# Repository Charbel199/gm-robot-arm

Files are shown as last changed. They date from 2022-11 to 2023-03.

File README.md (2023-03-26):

<p align="center">
  
</p>

--------------------------------------------------------------------

# GM Robot Arm

We are developing a robot arm system that is capable of playing chess. This is just a fun project meant to help us learn new thing.
Here is the simple action flow of the robot arm:
- Take a snapshot of the current chess-board layout using a top-down camera
- Deduce the previous made by the human by comparing the previous and current chessboard layouts using computer vision
- Choose the next best move using a chess engine
- Perform this move through autonomous control of the robot arm

Here is a [video demo](https://www.youtube.com/watch?v=iJfm-6d8eYs) showcasing our robot arm playing a full chess game (And winning).

## Installation

```bash
git clone https://github.com/Charbel199/gm-robot-arm
cd gm-robot-arm
pip install -r ./docker/requirements.txt # Will be later replaced with the actual docker container
```

### Azure Kinect Camera Setup
**Steps to use the azure kinect camera through docker**(_Note: Using the depth camera in docker requires OpenGL which we did not implement yet_)
1) Navigate to the AzureKinect directory
2) Run `. DockerBuild.bash`
3) Wait for the docker image to build 
4) Navigate back to the root of the repo
5) Run `. CameraRun.bash`
6) Using ROS, subscribe to the topic /rgb/image_raw for a BGRA format image 

## How to run it

Run each of the following commands in a separate terminal:
```bash
. CameraRun.bash
python3 ./cores/control_core.py
python3 main.py
```

There are some environment variables which can be set before running `main.py`:

- **USE_CAMERA**: this variable specifies if we want to use the camera or pre-existing images on the system (useful when the camera is not connected)
- **IS_SIMULATION**: this variable allows us to run the robot in simulation mode, where it simply follows a set of predetermined moves instead of evaluating the state of the board and playing the move deduced by the engine.
- **USE_ROBOT**: this variable allows us to run the system without actually using the robotic arm, which is valuable when testing other aspects of the system as the arm is time consuming.
- **WITH_SOUND**: allows the user to mute the clock sound if desired.
- **USE_PREVIOUS_CALIBRATED_BOARD**: this variable allows us to surpass the calibration phase in the case where we are playing in an environment where calibration has already taken place.
- **ENGINE_SIDE**: allows us to choose if the robot is playing as white or black.
- **ELO**: this variable determines what elo the engine will be using (valuable if the user is a beginner and would like to play against someone of the same skill)

To properly use the engine, the following sequence takes place in the gm core:

- Press ‘e’ to calibrate the board (this can be bypassed if the USE_PREVIOUS_CALIBRATED_BOARD environment variable is true). The gm core will then instruct the vision core to calibrate the board based on the current image. This must be done on an empty chess board.
- Press ‘i’ to take a snapshot of the initial board layout. This is important for the vision core to have a base image to start comparing to and figure out what moves were done. Make sure you have placed all the pieces before you press ‘i’.
- Start playing, and press ‘space’ when you complete your move.
  - The robot will make sure that it is the user's turn and that the previous steps (calibration and initialization) are complete.
  - It will launch the chess clock.
  - The gm core instructs the vision core to capture the current image.
  - It then instructs it to compare the previous board image to the current board image and determine which squares changed.
  - It then asks the chess core to determine which move was executed based on which squares changed.
  - It will update the virtual board state.
  - It then switches turn to the robots turn.
- Once it is the robots turn:
  - The gm core retrieves the best move from the chess core based on the current board state.
  - It then asks the chess core to dissect the best move into a sequence of moves that the control core can execute (PICKs, PLACEs, and YEETs)
  - The gm core then sets the control move counter based on how many control moves need to be completed for the entire move to be completed.
  - It then publishes all the moves on the topic that the control core is subscribed to.
  - The gm core waits until the move is fully executed (move counter is 0)
  - The gm core instructs the vision core to capture the current image.
  - It then instructs the chess core to update the virtual board.
  - Finally, it switches back to the user’s turn.

Some other features that can be done are pressing ‘v’ to visualize the last move as determined by vision and to press ‘b’ to visualize all images that the vision core is using. 

The final feature is the ‘esc’ key that allows us to reset the cores and start a game from scratch.

--------------------------------------------------------------------

## General architecture

The system is divided into **4 main components**: Chess core, vision core, control core and gm core. Each core has a set
of unique functionalities which we will discuss further in later parts.



Here is a communication diagram showing how the various components communicate with each other:

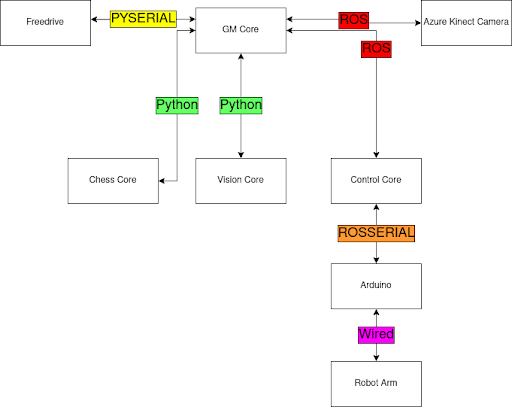
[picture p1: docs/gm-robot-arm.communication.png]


## Software Components

- Stockfish
- ROS
- OpenCV

## Hardware Components

- [6 DOF Robot arm (LeArm)](https://www.hiwonder.com/store/learn/2.html)
- Azure Kinect camera
- Arduino Mega 2560

_Note: The robotic arm used is intended for educational purposes, therefore, its servos are not the most accurate.
It would obviously have been better to use a more precise and expensive arm for better results._

_Note 2: The Azure kinect camera is way overkill for this project, but it was the camera we had at hand._

## Chess pieces

There chess pieces were designed on SOLIDWORK, here is a picture of the bishop 3d model:

<p align="center">
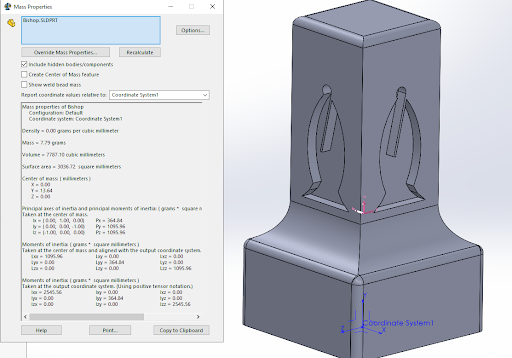
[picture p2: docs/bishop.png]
  
</p>

## Cores

### Chess Core

The chess core has two main functionalities:
- Visualize the current board layout
- Load a chess engine to generate moves for the robotic arm

Our chess visualizer makes use of the python **“chess”** package which 
provides us with a miniature **chess board svg** and can be fed moves 
to update the svg. We are using the resulting image to track the piece positions during the game.

<p align="center">
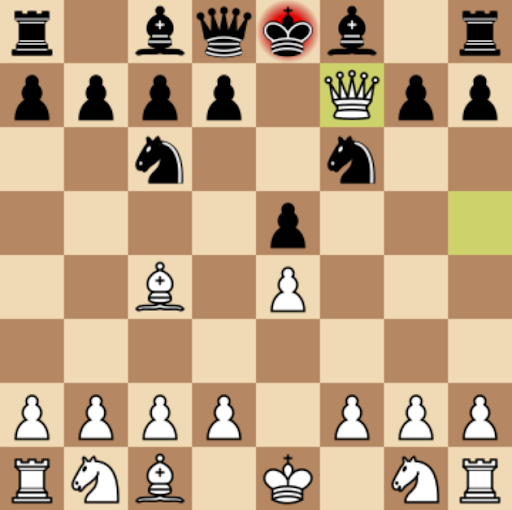
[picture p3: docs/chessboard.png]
  
</p>

### Vision Core

The main tasks of the vision core are to analyze the physical chess board, deduce the player’s move, and keep the chess pieces’ positions up to date.
We will briefly discuss the main functions that were implemented in the vision core:

- Preprocess image: This function is called each time we capture a new image. Based on the 4 markers in the corners of the chess board, it determines their coordinates and warps the image so that the chessboard is the only part of the image that is left.

<p align="center">
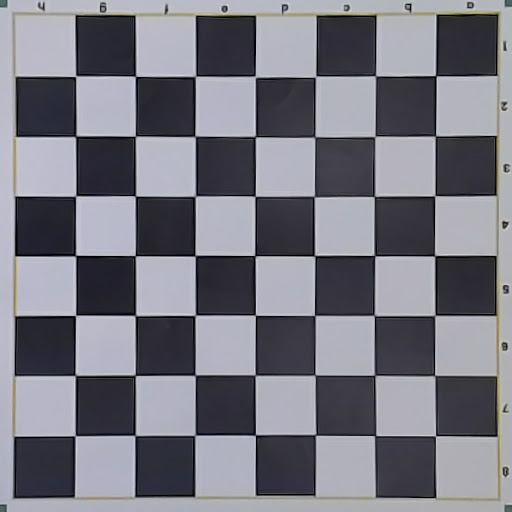
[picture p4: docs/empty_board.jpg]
  
</p>

- Visualize all images: Show up to the last 7 chess board snapshots (each representing a move) along with the calibrated board image.
- Visualize last move: Visualize the last 2 chess board snapshots with the move performed highlighted in red
- Calibrate: Uses the HSV threshold specified in the config json file located in the “assets/hsv” folder, the Vision core obtains the squares information after some image processing:
  - Get HSV filtered canny edges for white squares
  - Get HSV filtered canny edges for black squares
  - Combine both edge images
  <p align="center">
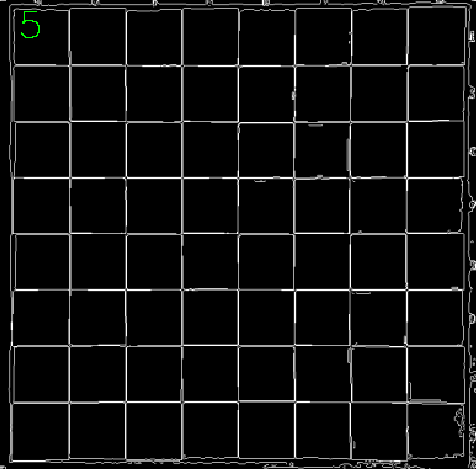
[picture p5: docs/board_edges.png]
    
  </p>
  
  - Perform Gaussian blur and threshold

  <p align="center">
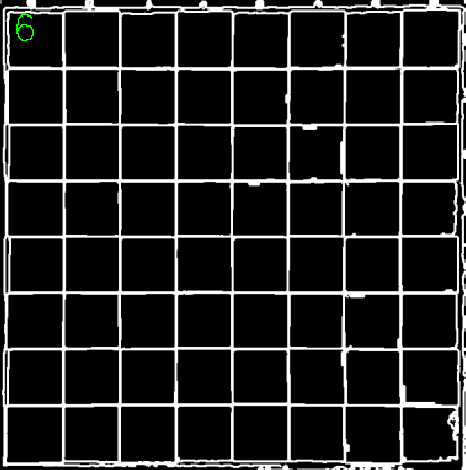
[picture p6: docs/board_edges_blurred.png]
    
  </p>

  - Find all possible contours and filter them based on the board size (We are assuming that each square has a minimum area of: (Wboard * Hboard / 64) and a maximum area of: minimum area * 1.3)

  <p align="center">
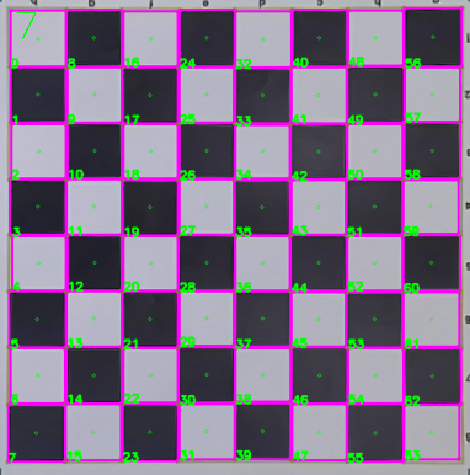
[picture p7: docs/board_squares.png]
    
  </p>

  - Reduce points meaning that since each square has 4 corners, many points will overlap, this step combines points that are very close to each other

- Capture image: Record the current image from the camera (Recorded through ROS in GM core
- Update images: Update the list of image (Keep the 7 most recent snapshots)
- Capture initial chess board layout: Set the next recorded image as the “Initial board layout” snapshot
- Get user squares changed: To deduce which squares have changed between the last 2 recorded snapshots, the vision core extracts color features from each square of both images and compares them, based on this comparison it can accurately determine which squares have changed. To explain this concept further: It is very inefficient to try to determine the type of piece that is present on each square on the board, alternatively, we are determining the DIFFERENCE between every 2 snapshots, and since we have a constant record of the pieces’ locations on the chess board, the system is able to deduce the next position on the chess board. (This is similar to how GITHUB works where each ‘delta’/difference is recorded with each commit and we are able to rollback to any previous version by simply reversing commits)
<p align="center">
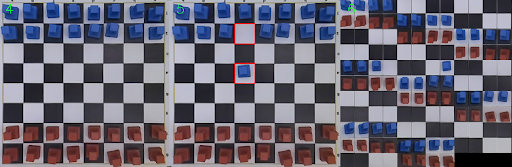
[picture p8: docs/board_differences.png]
  
</p>
Here is a screenshot showing the visualization generated by the vision core module:
<p align="center">
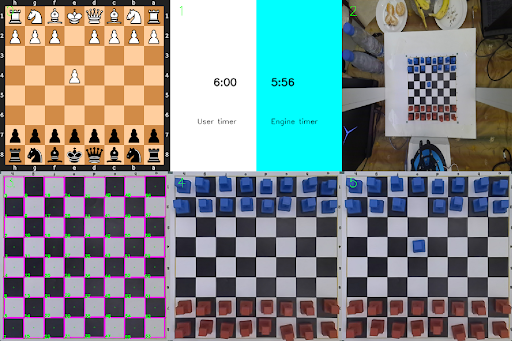
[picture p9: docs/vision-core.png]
  
</p>

### Control Core

The control core is mainly responsible for controlling the robotic arm. This core receives the move it's supposed to make on a rostopic in a custom message type called Move. This message contains two variables: type and square. The possible types are:

- PICK: specifies that we want the arm to pick the piece in the square.
- PLACE: specifies that we want the arm to place the piece it is carrying in the square.
- YEET: specifies that we want the arm to discard the piece it is carrying (used for taking a piece).

The square is simply a chess board square specified as ‘letterNumber’ such as ‘a5’.

The control core then accesses a python dictionary containing the sequence of moves that must be taken to go to a specific square. This dictionary has chess squares as its keys and a list of servo positions as its values. 

The core then publishes these servo positions onto a rostopic as a custom message type called ServoPositions. These positions are then written to the servos by arduino. The exact communication will be discussed in a later section. 

Let us take a full example of how the control core functions:

Consider that the chess core determines that the best move is for the pawn on square e5 to take the pawn on d4, the Move messages published by the gm core would be:

1) PICK D4
2) YEET 
3) PICK E5
4) PLACE D4

The control core would thus start with the message: [‘PICK’, ‘d4’]. It would access the move dictionary to know the servo positions corresponding to d4, and start publishing these positions to the arduino for the robot arm to move to d4. The type ‘PICK’ helps us determine that the gripper should be open initially, and should close once we are in the position d4. At the end of this move, we expect the arm to now have the pawn at d4 in its gripper.

Afterwards, the control core proceeds with the message [‘YEET’,’’]. This means that the arm will now simply go to the predetermined YEET_POSE and release the pawn it is carrying there.

Then, the control core processes the message [‘PICK’, ‘e5’]. Thus, the robotic arm is expected to go to square e5 and pick up the pawn there.

Finally, the control core proceeds with the last message [‘PLACE’, ‘d4’] in which it will place the pawn it is currently carrying on square d4, meaning the entire move is completed. At this point, the robotic arm will return to its SAFE_POSE which is a position that is away from the board and doesn’t impede the camera's field of view.

_Note that the arduino is publishing constantly to a topic to inform the control core it is done with the positions that were last sent to it, this allows the control core to send the other move. Additionally, the control core decrements a global parameter everytime a move is completed which helps the gm core determine if the entire move has been completed. In the previous example, this counter would be 4, and the control core will decrement it after every sequence, and once all 4 have been completed the gm core knows that the entire move is executed and can thus proceed._

### GM Core

The GM core, or the grandmaster core, is the “brain” of the robot. Its main function is to create and connect the other 3 cores and transmit messages between them.  It also creates the menu to be used by the user and takes his inputs through a keylogger. 

All the functionalities of the GM core were discussed in the [How to run it](#how-to-run-it) section where the environment variables and keyboard inputs were discussed. 

## Developers

- [Charbel Bou Maroun](https://github.com/Charbel199)
- [Georges Daou](https://github.com/George1044)
- [Ralph Sakhat](https://github.com/Ralph-S)

## License
This project is licensed under the MIT License. See the LICENSE file for details.

## Acknowledgements

We would like to thank [3D Maker shop](https://www.3dmakershop.com/) for sponsoring our project and helping us print all the chess pieces that we used.

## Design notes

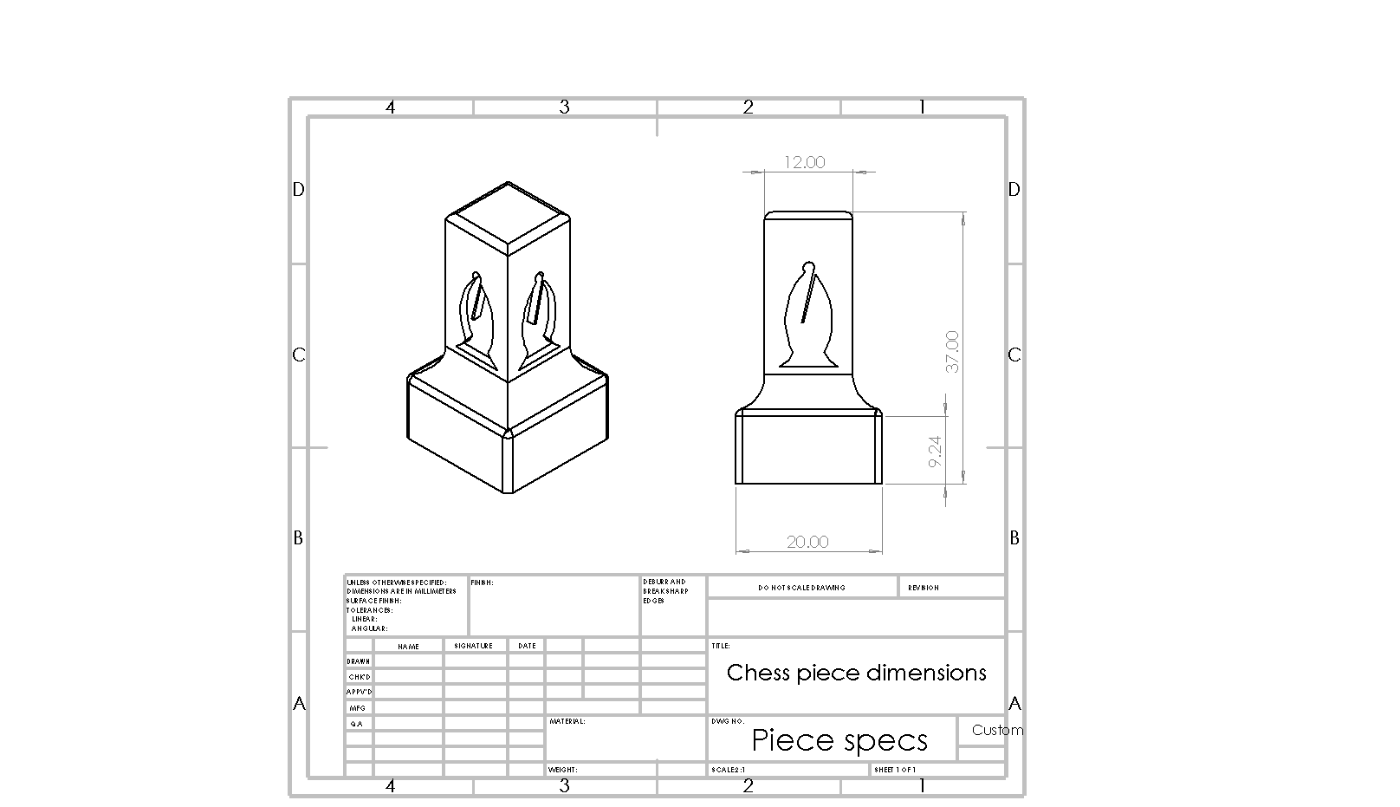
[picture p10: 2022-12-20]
src/arm/CAD/Chess pieces/Profiles/Piece specs.PNG

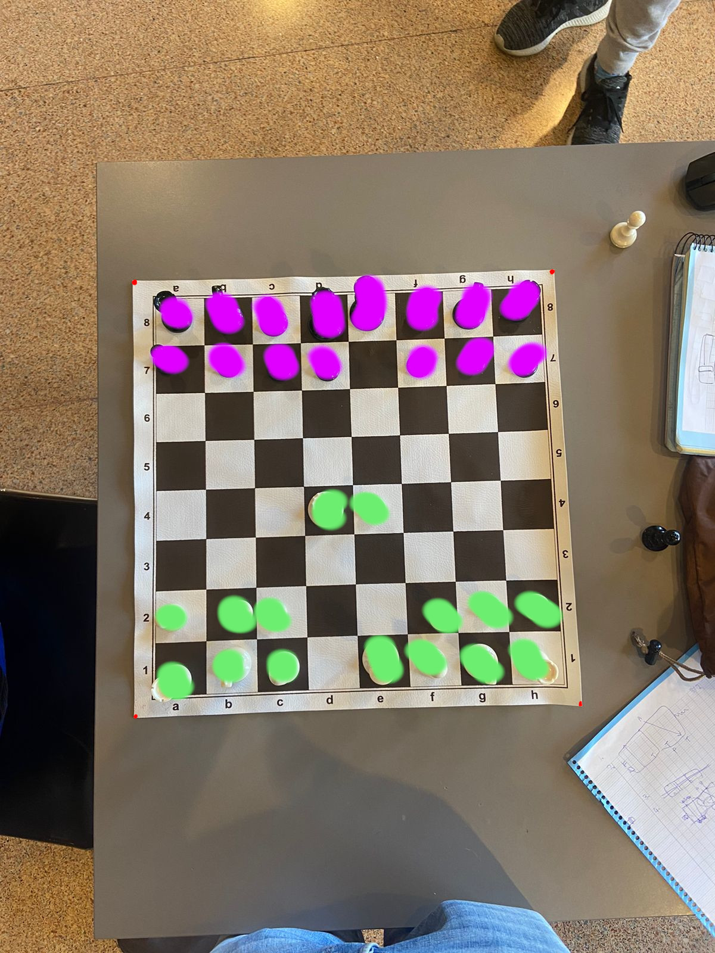
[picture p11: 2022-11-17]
src/assets/moves/real_board/colored/Move5.jpeg

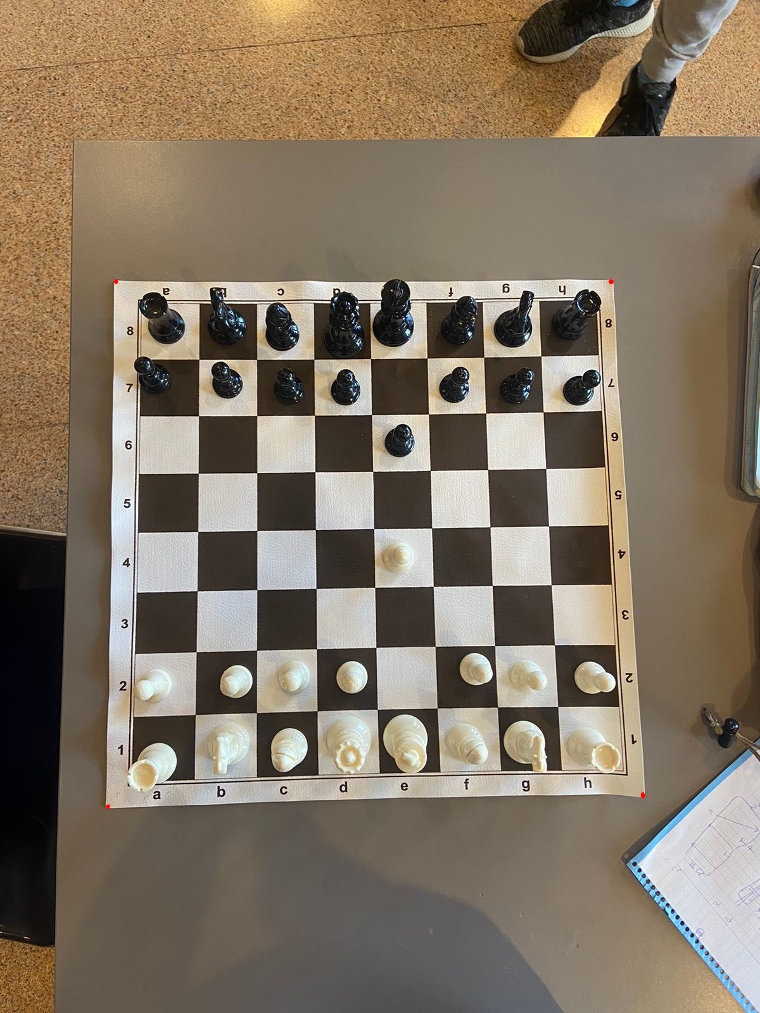
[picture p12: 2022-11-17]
src/assets/moves/real_board/Move2.jpeg

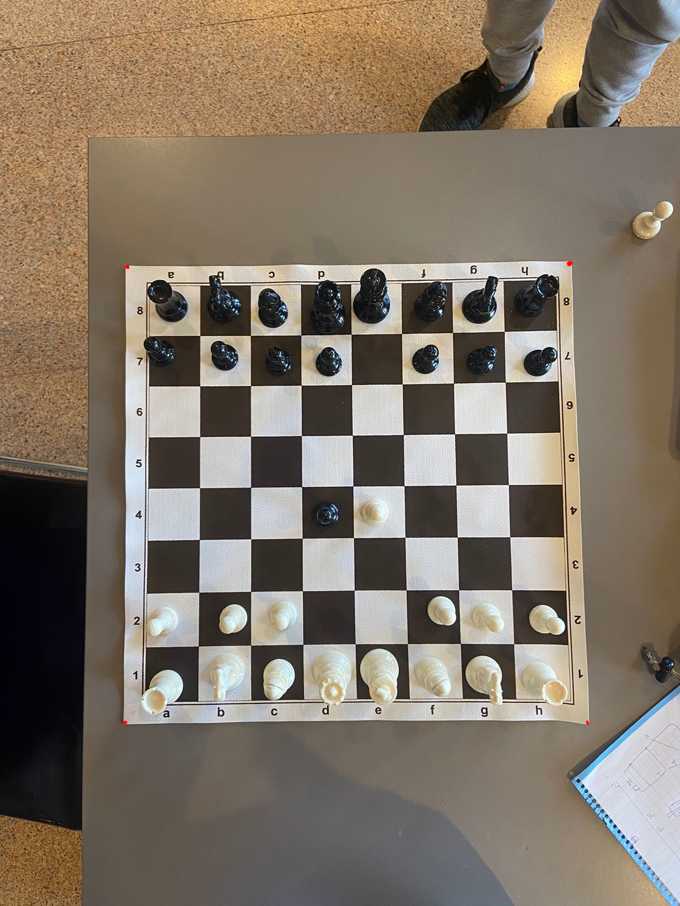
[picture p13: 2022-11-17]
src/assets/moves/real_board/Move4.jpeg

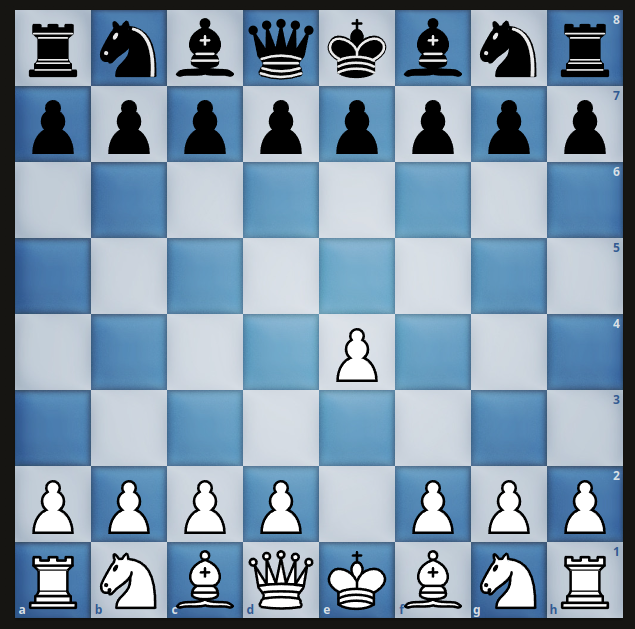
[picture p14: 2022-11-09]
src/assets/moves/lichess_2.png

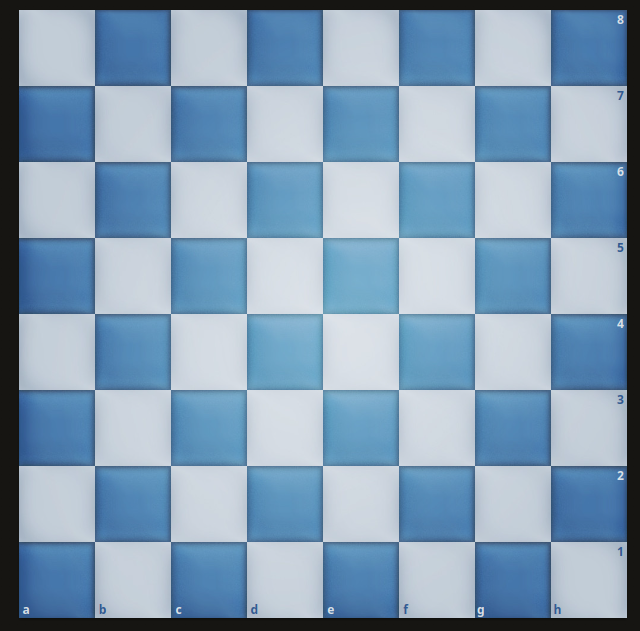
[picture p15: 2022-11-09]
src/assets/moves/empty_lichess2.png

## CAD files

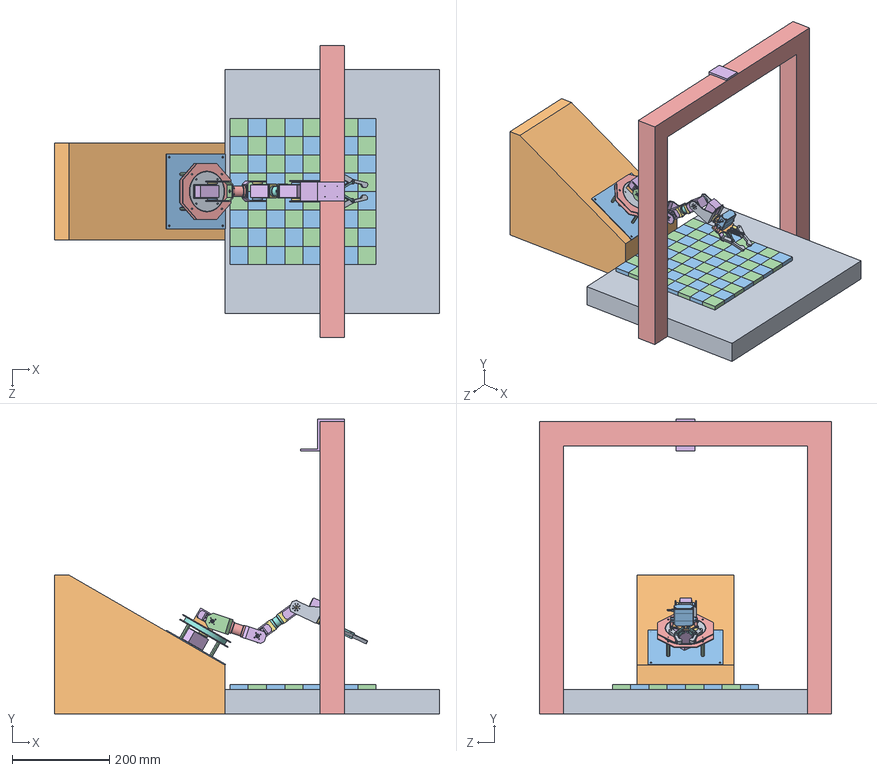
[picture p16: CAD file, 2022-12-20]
src/arm/CAD/Complete Assembly/Project Assembly.SLDASM
790.0 x 605.0 x 600.0 mm
BaseAssembly
RobotBase
BasePlate
SpacerNut x 4
RotaryAxisPolygonPlate x 2
LX-15D-LOBOT SERVO LEWANSOUL x 5
FrontHub x 6
RotaryAxisBearing
RotaryAxisDiskPlate x 2
LongServoSideBracket
BackHub x 3
Lower Pitch Bracket
29mm Union
Mid Pitch Bracket
ShortServoSideBracket x 2
20.5mm Union
Upper Pitch Bracket
GripperBasePlate
Lewansoul_LD-27MG Servo
M3 2.5mm length Spacer x 3
M3 11mm length Spacer x 4
GripperServoArmRightSide
GripperServoArmLeftSide
finger dog bone x 4
EndFinger x 4
ServoGriperHeadToGripperBaseBracket x 2
Black squares
White squares
CameraBase
CameraHolder

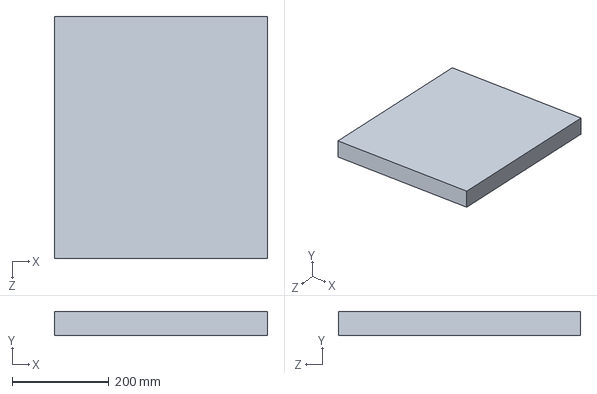
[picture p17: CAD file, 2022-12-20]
src/arm/CAD/Environment base/BaseAssembly.SLDPRT
440.0 x 50.0 x 500.0 mm

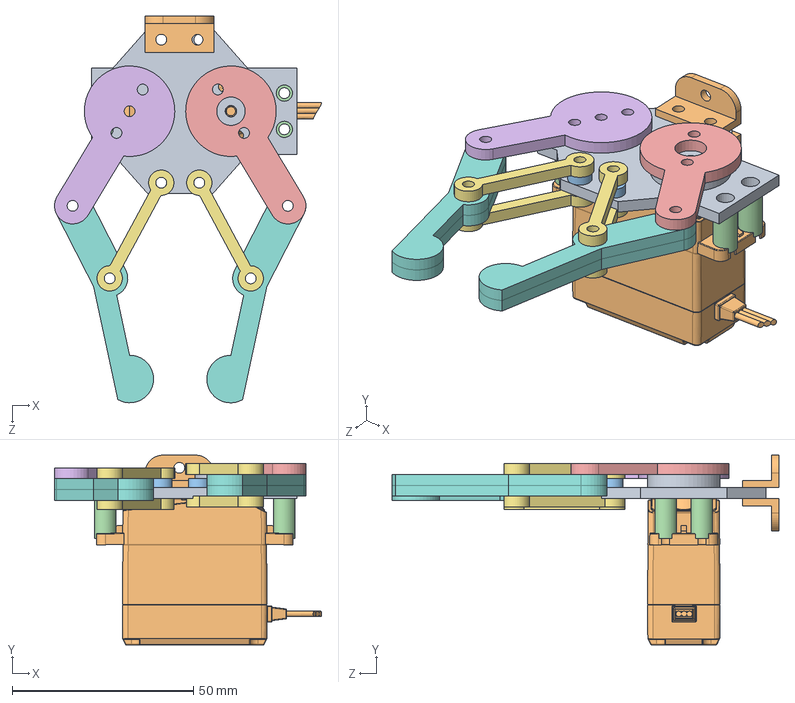
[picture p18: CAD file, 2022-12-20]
src/arm/CAD/robot assembly/GripperAssy.SLDASM
73.7 x 52.4 x 106.8 mm
GripperBasePlate
Lewansoul_LD-27MG Servo
M3 2.5mm length Spacer x 3
M3 11mm length Spacer x 4
GripperServoArmRightSide
GripperServoArmLeftSide
finger dog bone x 4
EndFinger x 4
FrontHub
ServoGriperHeadToGripperBaseBracket x 2

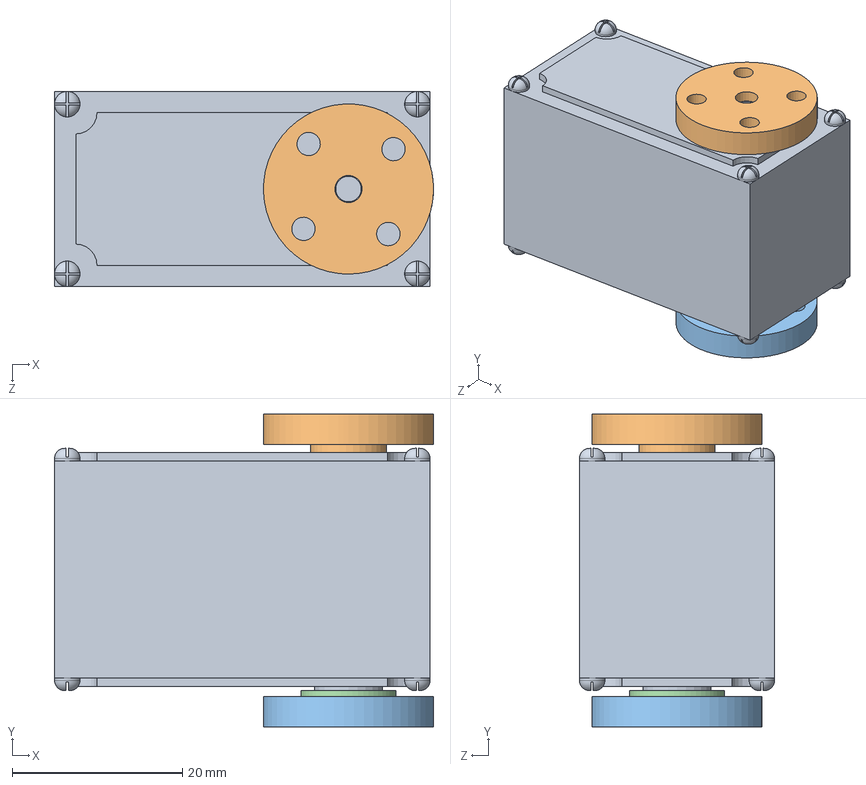
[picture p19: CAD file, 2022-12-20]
src/arm/CAD/robot assembly/LX-15D LOBOT Servo 2-Horns Assy.SLDASM
44.6 x 36.8 x 22.9 mm
LX-15D-LOBOT SERVO LEWANSOUL
FrontHub
BackHub
Bearing

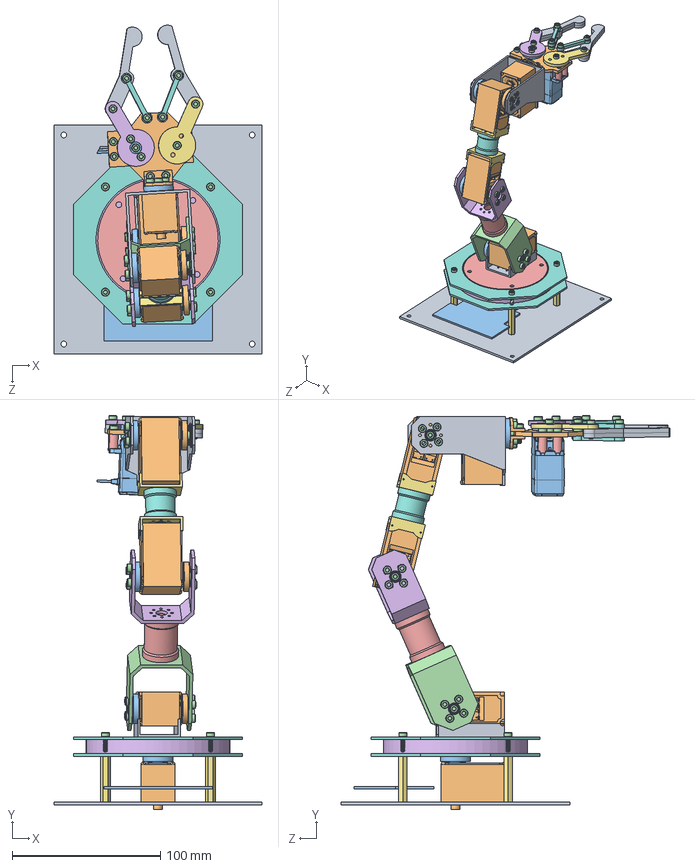
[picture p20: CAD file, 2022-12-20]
src/arm/CAD/robot assembly/LewanSoul LOBOT Arm Assy.SLDASM
140.3 x 265.8 x 221.8 mm
BasePlate
LX-15D-LOBOT SERVO LEWANSOUL x 5
FrontHub x 6
M3 5.5mm x 62
RotaryAxisDiskPlate x 2
RotaryAxisBearing
SpacerNut x 4
RotaryAxisPolygonPlate x 2
LongServoSideBracket
BackHub x 3
Bearing x 3
Lower Pitch Bracket
29mm Union
Mid Pitch Bracket
ShortServoSideBracket x 2
20.5mm Union
Upper Pitch Bracket
GripperBasePlate
Lewansoul_LD-27MG Servo
M3 2.5mm length Spacer x 3
M3 11mm length Spacer x 4
GripperServoArmRightSide
GripperServoArmLeftSide
finger dog bone x 4
EndFinger x 4
ServoGriperHeadToGripperBaseBracket x 2
ArmControllerBoard

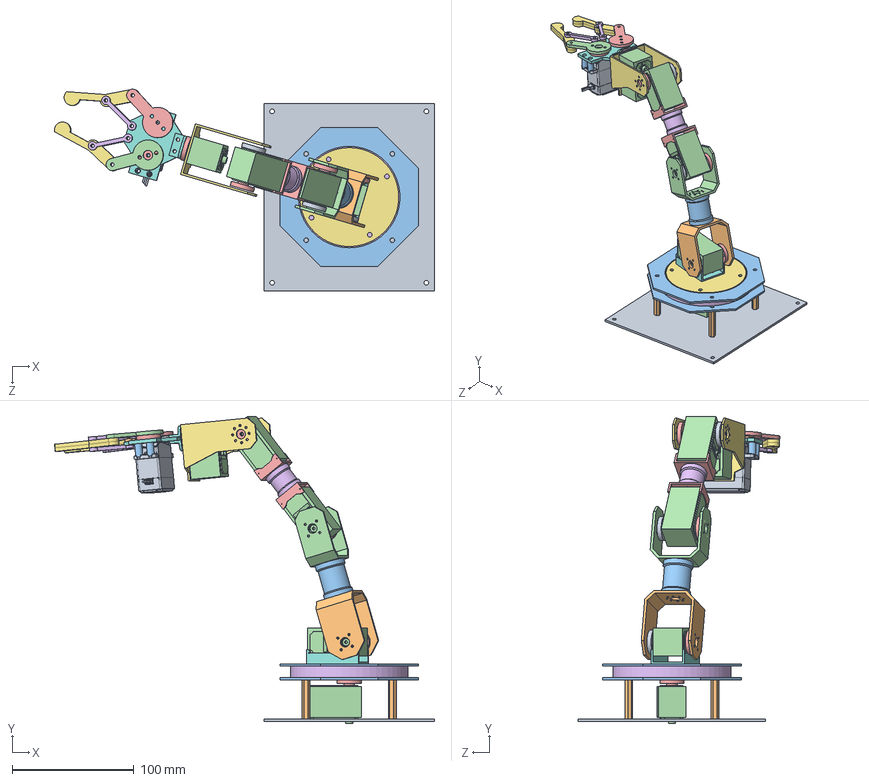
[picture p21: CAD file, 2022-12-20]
src/arm/CAD/Robot Arm Assembly/NewAssembly.SLDASM
312.7 x 252.9 x 165.9 mm
BasePlate
SpacerNut x 4
RotaryAxisPolygonPlate x 2
LX-15D-LOBOT SERVO LEWANSOUL x 5
FrontHub x 6
RotaryAxisBearing
RotaryAxisDiskPlate x 2
LongServoSideBracket
BackHub x 3
Lower Pitch Bracket
29mm Union
Mid Pitch Bracket
ShortServoSideBracket x 2
20.5mm Union
Upper Pitch Bracket
GripperBasePlate
Lewansoul_LD-27MG Servo
M3 2.5mm length Spacer x 3
M3 11mm length Spacer x 4
GripperServoArmRightSide
GripperServoArmLeftSide
finger dog bone x 4
EndFinger x 4
ServoGriperHeadToGripperBaseBracket x 2

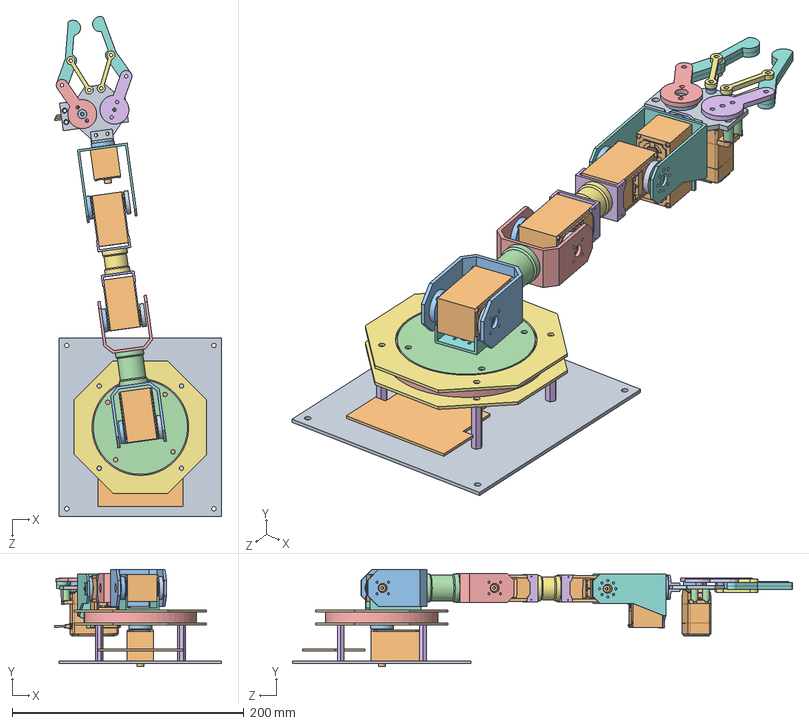
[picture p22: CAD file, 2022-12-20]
src/arm/CAD/robot assembly/LewanSoul LOBOT Arm Assy at legth.SLDASM
144.4 x 84.0 x 431.6 mm
BasePlate
LX-15D-LOBOT SERVO LEWANSOUL x 5
FrontHub x 6
RotaryAxisDiskPlate x 2
RotaryAxisBearing
SpacerNut x 4
RotaryAxisPolygonPlate x 2
LongServoSideBracket
BackHub x 3
Bearing x 3
Lower Pitch Bracket
29mm Union
Mid Pitch Bracket
ShortServoSideBracket x 2
20.5mm Union
Upper Pitch Bracket
GripperBasePlate
Lewansoul_LD-27MG Servo
M3 2.5mm length Spacer x 3
M3 11mm length Spacer x 4
GripperServoArmRightSide
GripperServoArmLeftSide
finger dog bone x 4
EndFinger x 4
ServoGriperHeadToGripperBaseBracket x 2
ArmControllerBoard

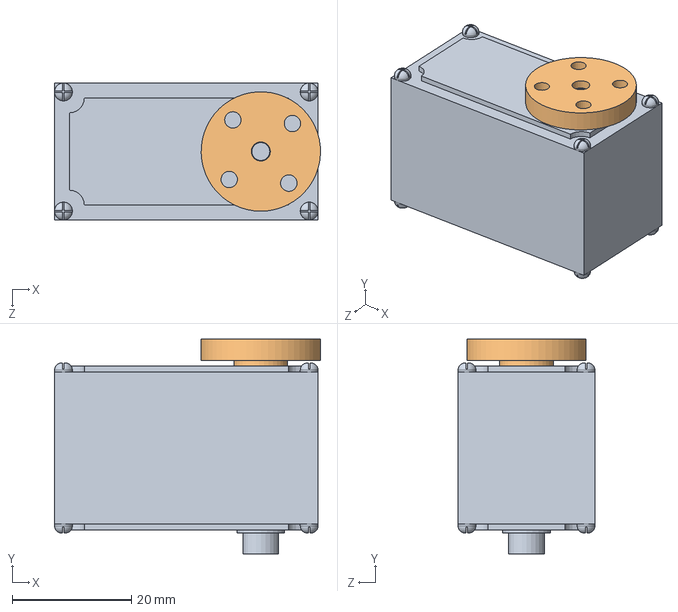
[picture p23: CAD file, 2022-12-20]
src/arm/CAD/robot assembly/LX-15D LOBOT Servo 1-Horn Assy.SLDASM
44.6 x 36.0 x 22.9 mm
LX-15D-LOBOT SERVO LEWANSOUL
FrontHub

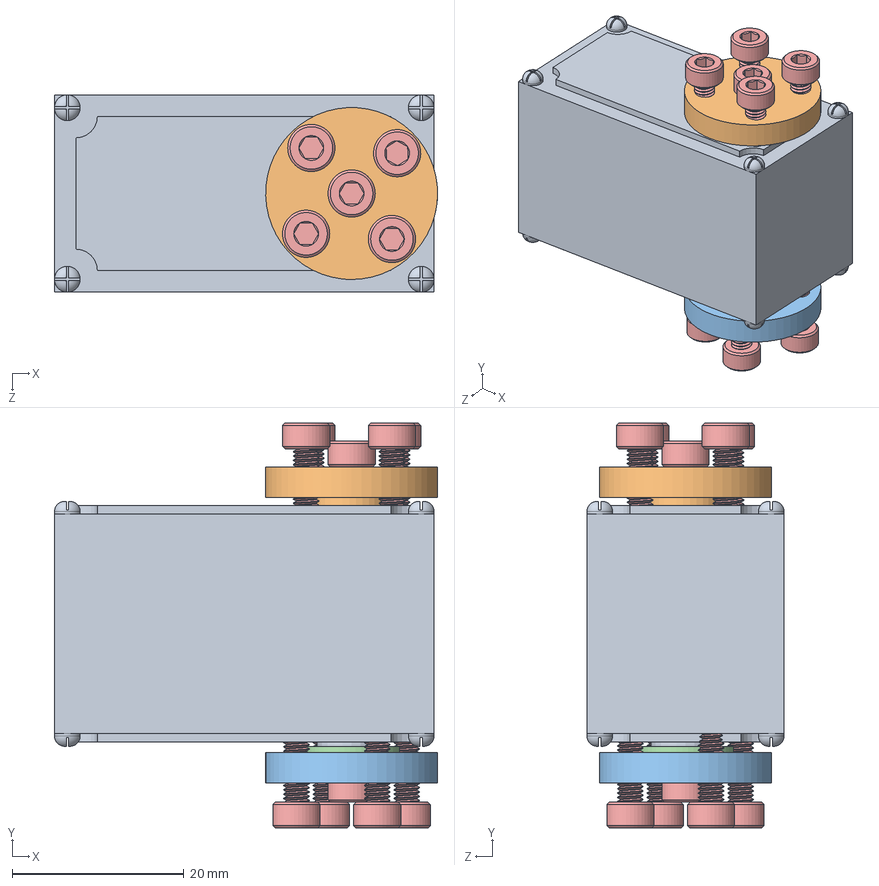
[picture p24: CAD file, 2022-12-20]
src/arm/CAD/robot assembly/LX-15D LOBOT SERVO ASSY.SLDASM
44.6 x 47.1 x 22.9 mm
LX-15D-LOBOT SERVO LEWANSOUL
FrontHub
BackHub
Bearing
M3 5.5mm x 10

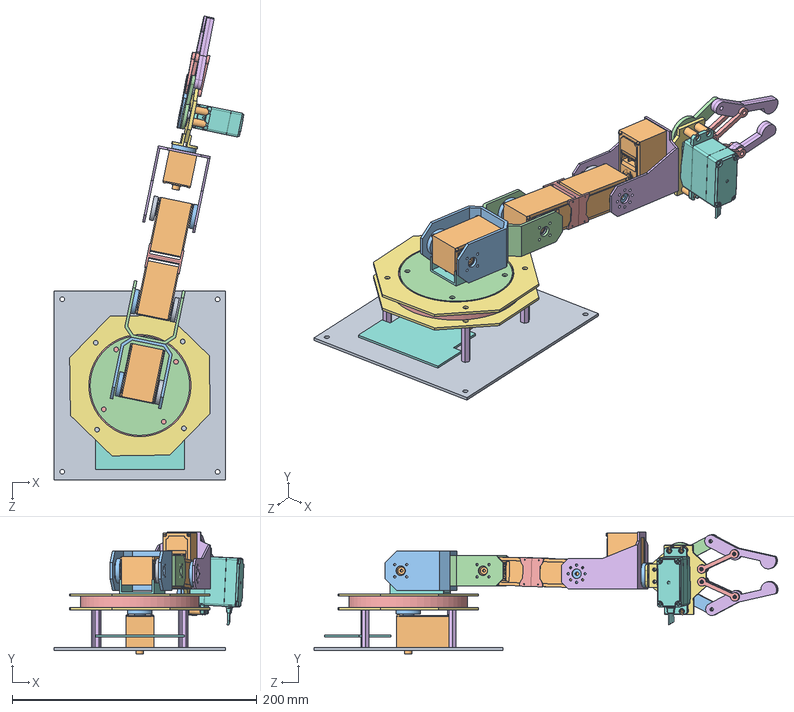
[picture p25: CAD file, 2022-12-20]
src/arm/CAD/robot assembly/LewanSoul LOBOT Arm Assy modified union parallel.SLDASM
155.2 x 99.5 x 379.2 mm
BasePlate
LX-15D-LOBOT SERVO LEWANSOUL x 5
FrontHub x 6
RotaryAxisDiskPlate x 2
RotaryAxisBearing
SpacerNut x 4
RotaryAxisPolygonPlate x 2
LongServoSideBracket
BackHub x 3
Bearing x 3
Lower Pitch Bracket
Mid Pitch Bracket
ShortServoSideBracket x 2
Upper Pitch Bracket
GripperBasePlate
Lewansoul_LD-27MG Servo
M3 2.5mm length Spacer x 3
M3 11mm length Spacer x 4
GripperServoArmRightSide
GripperServoArmLeftSide
finger dog bone x 4
EndFinger x 4
ServoGriperHeadToGripperBaseBracket x 2
ArmControllerBoard

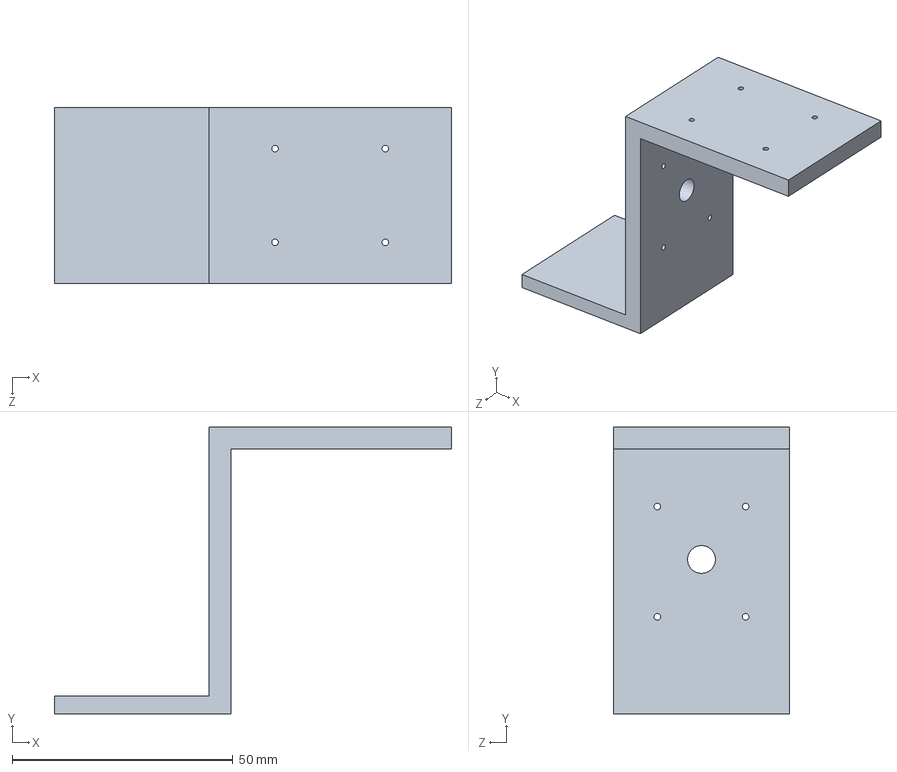
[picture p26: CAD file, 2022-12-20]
src/arm/CAD/Camera Holder/CameraHolder.SLDPRT
90.0 x 65.0 x 40.0 mm

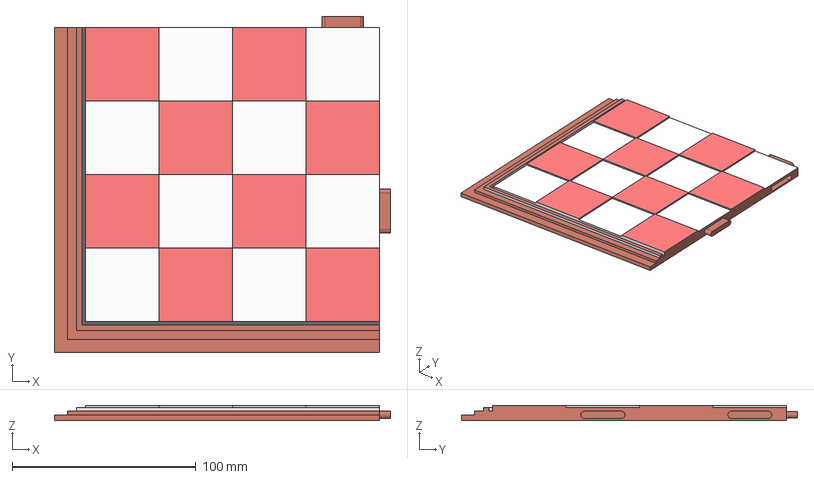
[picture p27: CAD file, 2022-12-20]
src/arm/CAD/chess board/chess board 2 (x2).stp
183.0 x 183.0 x 8.00 mm

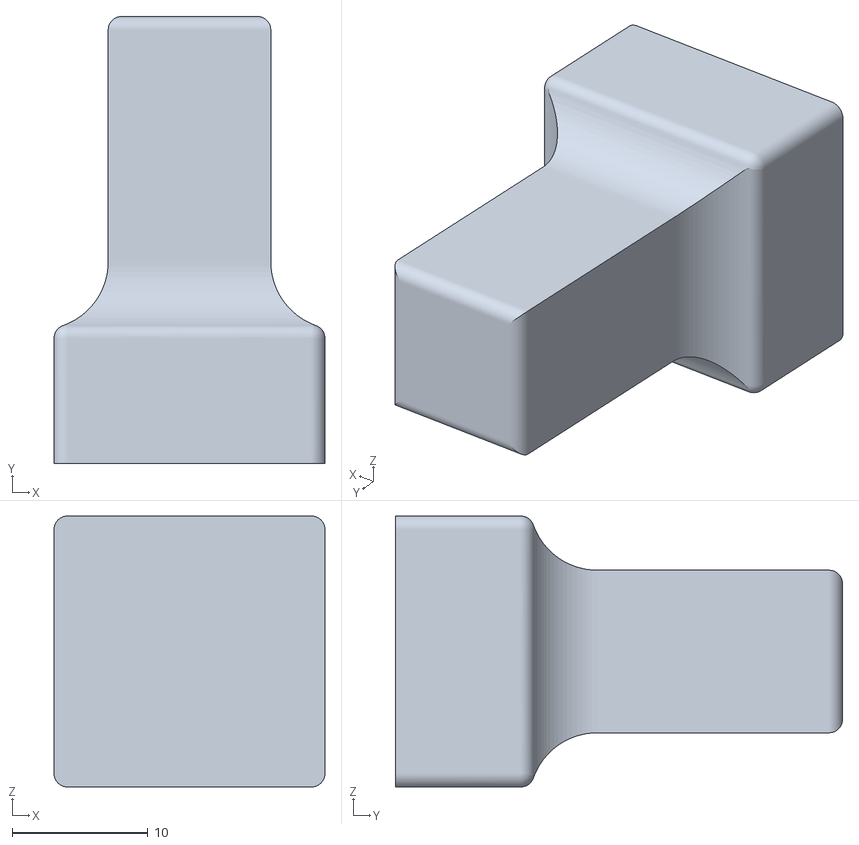
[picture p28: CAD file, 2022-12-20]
src/arm/CAD/Chess pieces/ChessPiece12-33.STL
20.0 x 33.0 x 20.0

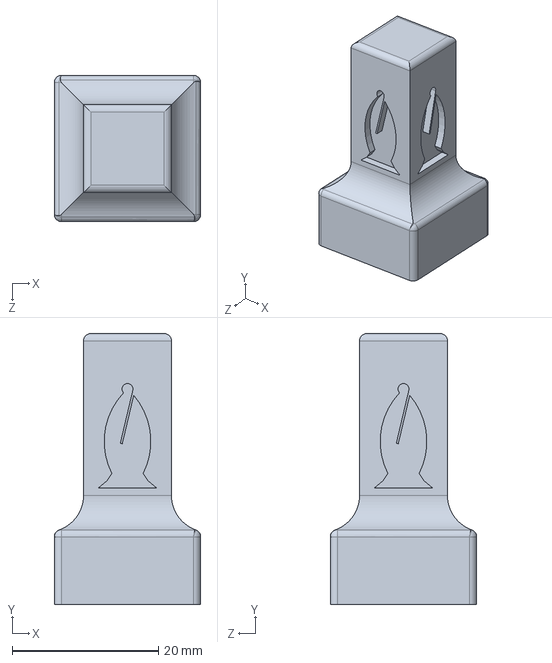
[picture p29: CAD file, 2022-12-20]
src/arm/CAD/Chess pieces/Profiles/Bishop.SLDPRT
20.0 x 37.0 x 20.0 mm

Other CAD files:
src/arm/CAD/New Chess Board/White squares.SLDPRT
src/arm/CAD/Robot Arm Assembly/BackHub .SLDPRT
src/arm/CAD/robot assembly/ShortServoSideBracket.SLDPRT
src/arm/CAD/Camera Holder/CameraBase.SLDPRT
src/arm/CAD/Camera Holder/CameraHolder.STL
src/arm/CAD/Chess pieces/ChessPiece.SLDPRT
src/arm/CAD/Chess pieces/ChessPiece12-35.STL
src/arm/CAD/Chess pieces/ChessPiece12-37.STL
src/arm/CAD/Chess pieces/ChessPiece33.STL
src/arm/CAD/Chess pieces/ChessPiece35.STL
src/arm/CAD/Chess pieces/ChessPiece37.STL
src/arm/CAD/Chess pieces/GenericPiece.SLDDRW
src/arm/CAD/Chess pieces/GenericPiece.SLDPRT
src/arm/CAD/Chess pieces/GenericPiece.STL
src/arm/CAD/Chess pieces/Profiles/Bishop.STL
src/arm/CAD/Chess pieces/Profiles/Caballo ajedrez 2D.dwg
src/arm/CAD/Chess pieces/Profiles/King.SLDPRT
src/arm/CAD/Chess pieces/Profiles/King.STL
src/arm/CAD/Chess pieces/Profiles/Knight.SLDPRT
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

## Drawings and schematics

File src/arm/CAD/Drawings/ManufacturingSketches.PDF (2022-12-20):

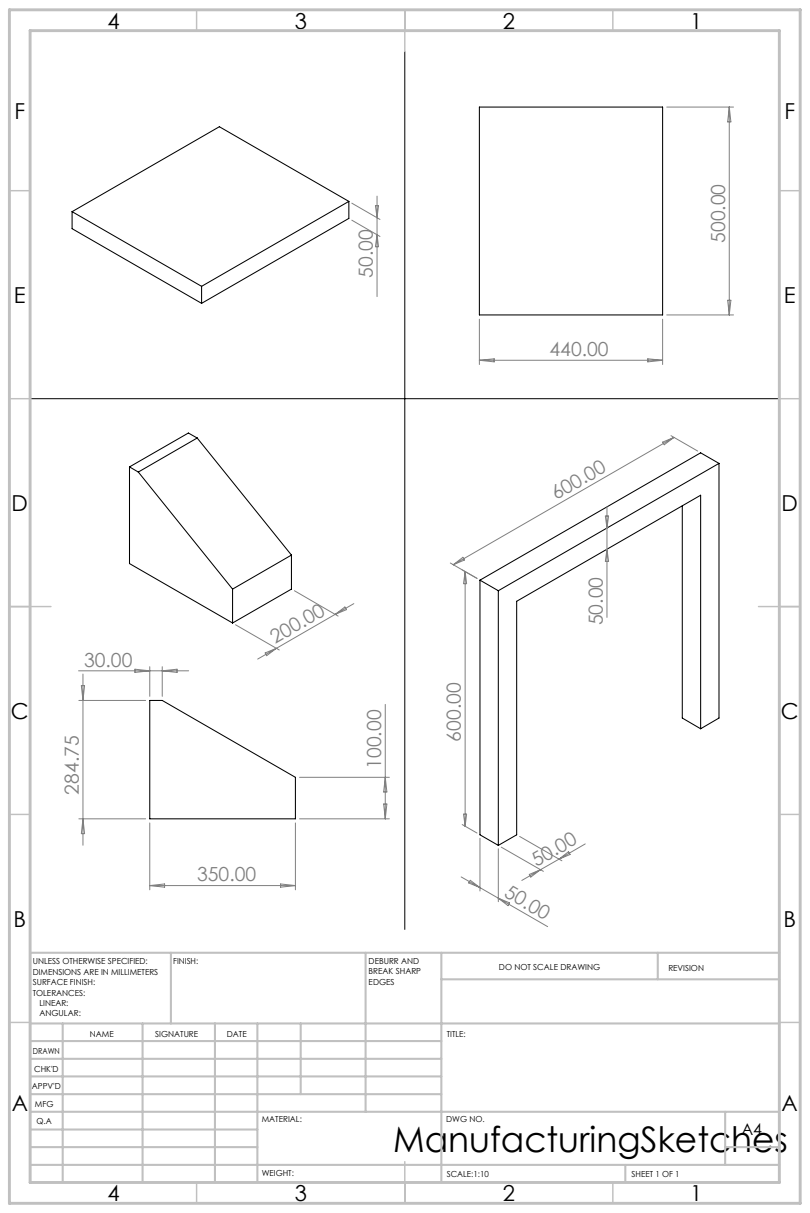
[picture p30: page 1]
FINISH:; DEBURR AND; BREAK SHARP; DO NOT SCALE DRAWING; REVISION; SCALE:1:10; SHEET 1 OF 1

UNLESS OTHERWISE SPECIFIED:
DIMENSIONS ARE IN MILLIMETERS
SURFACE FINISH:
TOLERANCES:
LINEAR:
ANGULAR:

NAME | SIGNATURE | DATE | | | | TITLE:

DRAWN
CHK'D
APPV'D
MFG
Q.A | | | | MATERIAL: ManufacturingSketches | DWG NO. | A4

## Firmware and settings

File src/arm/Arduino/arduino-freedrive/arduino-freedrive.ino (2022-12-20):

#include <Servo.h>
#define servoPin1 7
#define servoPin2 2
#define servoPin3 3
#define servoPin4 4
#define servoPin5 5
#define servoPin6 6

Servo servo1;   //Range: 90 to 180
Servo servo2;   //Range: 0 to 180
Servo servo3;   //Range: 0 to 180 
Servo servo4;   //Range: 0 to 180
Servo servo5;   //Range: 0 to 180
Servo servo6;   //Range: 0 to 180

#define DELAY 5
#define SERVO_STEP 5
#define SERVO_STEP_SMALL 2

#define servo1_safe 146
#define servo2_safe 0
#define servo3_safe 90
#define servo4_safe 0
#define servo5_safe 180
#define servo6_safe 90

int x;
String instruction;
String str;
char move_instruction;
float servo1_pos;
float servo2_pos;
float servo3_pos;
float servo4_pos;
float servo5_pos;
float servo6_pos;
int servo;
String servo_positions = "";
int value;


void setup() {
  Serial.begin(9600);
  pinMode(13, OUTPUT);
  servo1.attach(servoPin1);
  servo1.write(servo1_safe);
  servo2.attach(servoPin2);
  servo2.write(servo2_safe);
  servo3.attach(servoPin3);
  servo3.write(servo3_safe);
  servo4.attach(servoPin4);
  servo4.write(servo4_safe);
  servo5.attach(servoPin5);
  servo5.write(servo5_safe);
  servo6.attach(servoPin6);
  servo6.write(servo6_safe);
  Serial.setTimeout(1);
}

void loop() {
  free_drive_control();
}

void moveServo(Servo servoX, int from, int to, int delayValue){
  if(to>=0 && to<=180){
    if(from > to){
        for(int i=from; i>to; i--){
            servoX.write(i);
            delay(delayValue);
            }
           }


  if(from < to){
  for(int i=from; i<to; i++){
    servoX.write(i);
    delay(delayValue);
  }
  }
  }
}


void manual_control(){
 while (!Serial.available());      // Loop till arduino receives a message
  instruction = Serial.readString();
  servo1_pos = servo1.read();
  servo2_pos = servo2.read();
  servo3_pos = servo3.read();
  servo4_pos = servo4.read();
  servo5_pos = servo5.read();
  servo6_pos = servo6.read();

  if(instruction == "R"){
      digitalWrite(13,HIGH);
      delay(250);
      digitalWrite(13,LOW);
      delay(250);
      servo_positions = "";
      servo_positions = servo_positions + "Servo 1: " + servo1_pos + "\t[" + servo2_pos + ", " + servo3_pos + ", " + servo4_pos + ", " + servo5_pos + ", " + servo6_pos +"]"; //stupid arduino string concatenation
      Serial.println(servo_positions);
    }
  else if(instruction == "W"){
      digitalWrite(13,HIGH);
      delay(250);
      digitalWrite(13,LOW);
      delay(250);
      while (!Serial.available()); //waiting for servo
      str = Serial.readString();
      //servo = str.toInt();
      servo = 1;
      Serial.println("Moving servo " + str);
      while (!Serial.available()); //waiting for angle
      str = Serial.readString();
      //value = str.toInt();
      value = 120;
      Serial.println("Going to angle " + str);
      switch(servo) {
        case 1: moveServo(servo1, servo1_pos, value, DELAY);
        break;
        case 2: moveServo(servo2, servo2_pos, value, DELAY);
        break;
        case 3: moveServo(servo3, servo3_pos, value, DELAY);
        break;
        case 4: moveServo(servo4, servo4_pos, value, DELAY);
        break;
        case 5: moveServo(servo5, servo5_pos, value, DELAY);
        break;
        case 6: moveServo(servo6, servo6_pos, value, DELAY);
        break;
        default:
        break;
        }
      Serial.println("Done");
    }
   }

void free_drive_control(){
  
  servo1_pos = servo1.read();
  servo2_pos = servo2.read();
  servo3_pos = servo3.read();
  servo4_pos = servo4.read();
  servo5_pos = servo5.read();
  servo6_pos = servo6.read();
  servo_positions = "";
  servo_positions = servo_positions + "Servo 1: " + servo1_pos + "\t[" + servo2_pos + ", " + servo3_pos + ", " + servo4_pos + ", " + servo5_pos + ", " + servo6_pos +"]"; //stupid arduino string concatenation
  Serial.println(servo_positions);
  while (!Serial.available());      // Loop till arduino receives a message
  move_instruction = Serial.read(); // String to char stupid 
  Serial.println(move_instruction);

  switch(move_instruction){
    case 'q': moveServo(servo1, servo1_pos, servo1_pos+SERVO_STEP, DELAY);
    break;
    case 'a': moveServo(servo1, servo1_pos, servo1_pos-SERVO_STEP, DELAY);
    break;

    case 'w': moveServo(servo2, servo2_pos, servo2_pos+SERVO_STEP, DELAY);
    break;
    case 's': moveServo(servo2, servo2_pos, servo2_pos-SERVO_STEP, DELAY);
    break;

    case 'e': moveServo(servo3, servo3_pos, servo3_pos+SERVO_STEP, DELAY);
    break;
    case 'd': moveServo(servo3, servo3_pos, servo3_pos-SERVO_STEP, DELAY);
    break;

    case 'r': moveServo(servo4, servo4_pos, servo4_pos+SERVO_STEP, DELAY);
    break;
    case 'f': moveServo(servo4, servo4_pos, servo4_pos-SERVO_STEP, DELAY);
    break;

    case 't': moveServo(servo5, servo5_pos, servo5_pos+SERVO_STEP, DELAY);
    break;
    case 'g': moveServo(servo5, servo5_pos, servo5_pos-SERVO_STEP, DELAY);
    break;

    case 'y': moveServo(servo6, servo6_pos, servo6_pos+SERVO_STEP, DELAY);
    break;
    case 'h': moveServo(servo6, servo6_pos, servo6_pos-SERVO_STEP, DELAY);
    break;

     case '1': moveServo(servo1, servo1_pos, servo1_pos+SERVO_STEP_SMALL, DELAY);
    break;
    case 'z': moveServo(servo1, servo1_pos, servo1_pos-SERVO_STEP_SMALL, DELAY);
    break;

    case '2': moveServo(servo2, servo2_pos, servo2_pos+SERVO_STEP_SMALL, DELAY);
    break;
    case 'x': moveServo(servo2, servo2_pos, servo2_pos-SERVO_STEP_SMALL, DELAY);
    break;

    case '3': moveServo(servo3, servo3_pos, servo3_pos+SERVO_STEP_SMALL, DELAY);
    break;
    case 'c': moveServo(servo3, servo3_pos, servo3_pos-SERVO_STEP_SMALL, DELAY);
    break;

    case '4': moveServo(servo4, servo4_pos, servo4_pos+SERVO_STEP_SMALL, DELAY);
    break;
    case 'v': moveServo(servo4, servo4_pos, servo4_pos-SERVO_STEP_SMALL, DELAY);
    break;

    case '5': moveServo(servo5, servo5_pos, servo5_pos+SERVO_STEP_SMALL, DELAY);
    break;
    case 'b': moveServo(servo5, servo5_pos, servo5_pos-SERVO_STEP_SMALL, DELAY);
    break;

    case '6': moveServo(servo6, servo6_pos, servo6_pos+SERVO_STEP_SMALL, DELAY);
    break;
    case 'n': moveServo(servo6, servo6_pos, servo6_pos-SERVO_STEP_SMALL, DELAY);
    break;
  }
  
  Serial.println("Done");
  }
   

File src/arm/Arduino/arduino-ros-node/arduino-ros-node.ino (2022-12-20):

#include <Servo.h>
#include <ros.h>
#include <rosserial_msgs/ServoPositions.h>
#include <std_msgs/Bool.h>

#define servoPin1 7
#define servoPin2 2
#define servoPin3 3
#define servoPin4 4
#define servoPin5 5
#define servoPin6 6

Servo servo1;   //Range: 90 to 180
Servo servo2;   //Range: 0 to 180
Servo servo3;   //Range: 0 to 180 
Servo servo4;   //Range: 0 to 180
Servo servo5;   //Range: 0 to 180
Servo servo6;   //Range: 0 to 180

#define EPSILON 1
#define DELAY 3

//SafePoseValues:
#define servo1_safe 142
#define servo2_safe 0
#define servo3_safe 90
#define servo4_safe 0
#define servo5_safe 180
#define servo6_safe 90


ros::NodeHandle nh;
std_msgs::Bool bool_msg;

ros::Publisher pub("control/move_done", &bool_msg);

void message(const rosserial_msgs::ServoPositions& servo_positions){
  nh.loginfo("RECEIVED MOVE");

  //Desired positions
  int servo1_des_pos = servo_positions.servo1;
  int servo2_des_pos = servo_positions.servo2;
  int servo3_des_pos = servo_positions.servo3;
  int servo4_des_pos = servo_positions.servo4;
  int servo5_des_pos = servo_positions.servo5;
  int servo6_des_pos = servo_positions.servo6;

  // Current positions
  float servo1_pos = servo1.read();

  char servo1_pos_str[6];
  char servo1_des_pos_str[4];
  char servo2_des_pos_str[4];
  char servo3_des_pos_str[4];
  char servo4_des_pos_str[4];
  char servo5_des_pos_str[4];
  char servo6_des_pos_str[4];
  //dtostrf(servo1_pos,2,2,servo1_pos_str);
  //nh.loginfo(servo1_pos_str);

  
  float servo2_pos = servo2.read();
  float servo3_pos = servo3.read();
  float servo4_pos = servo4.read();
  float servo5_pos = servo5.read();
  float servo6_pos = servo6.read();

  //flash LED
  digitalWrite(13, HIGH);   
  delay(250);             
  
  if(abs(servo6_des_pos - servo6_pos) > EPSILON){
  moveServo(servo6, servo6_pos, servo6_des_pos, DELAY*4);
  String(servo6_des_pos).toCharArray(servo6_des_pos_str,4);
  nh.loginfo(servo6_des_pos_str);
  }
  
  if(abs(servo5_des_pos - servo5_pos) > EPSILON){
  moveServo(servo5, servo5_pos, servo5_des_pos, DELAY*6);
  String(servo5_des_pos).toCharArray(servo5_des_pos_str,4);
  nh.loginfo(servo5_des_pos_str);
  }
  
  if(abs(servo4_des_pos - servo4_pos) > EPSILON){
  moveServo(servo4, servo4_pos, servo4_des_pos, DELAY*2);
  String(servo4_des_pos).toCharArray(servo4_des_pos_str,4);
  nh.loginfo(servo4_des_pos_str);
  }
  
  if(abs(servo3_des_pos - servo3_pos) > EPSILON){
  moveServo(servo3, servo3_pos, servo3_des_pos, DELAY*2);
  String(servo3_des_pos).toCharArray(servo3_des_pos_str,4);
  nh.loginfo(servo3_des_pos_str);
  }
    
  if(abs(servo2_des_pos - servo2_pos) > EPSILON){
  moveServo(servo2, servo2_pos, servo2_des_pos, DELAY);
  String(servo2_des_pos).toCharArray(servo2_des_pos_str,4);;
  nh.loginfo(servo2_des_pos_str);
  }
  
  if(abs(servo1_des_pos - servo1_pos) > EPSILON){
  moveServo(servo1, servo1_pos, servo1_des_pos, DELAY*5);
  String(servo1_des_pos).toCharArray(servo1_des_pos_str,4);
  nh.loginfo(servo1_des_pos_str);
  }
    
       
  digitalWrite(13, LOW); 
  pub.publish(&bool_msg);
  nh.loginfo("COMPLETED MOVE");
  }

 ros::Subscriber<rosserial_msgs::ServoPositions> controller("control/arm", &message);
 
void setup() { 
  pinMode(13, OUTPUT);
  servo1.attach(servoPin1);
  servo1.write(servo1_safe);
  servo2.attach(servoPin2);
  servo2.write(servo2_safe);
  servo3.attach(servoPin3);
  servo3.write(servo3_safe);
  servo4.attach(servoPin4);
  servo4.write(servo4_safe);
  servo5.attach(servoPin5);
  servo5.write(servo5_safe);
  servo6.attach(servoPin6);
  servo6.write(servo6_safe);
  
  nh.loginfo("1");
  nh.initNode();
  nh.loginfo("2");
  nh.advertise(pub);
  nh.logdebug("3");
  bool_msg.data = true;
  nh.subscribe(controller);
  nh.logdebug("INITIALIZED NODE");
  //goToInitialPose();
} 
 
 
void loop() {
   nh.spinOnce();
   delay(50);
   
}

void moveServo(Servo servoX, int from, int to, int delayValue){
  if(from > to){
  for(int i=from; i>to; i--){
    servoX.write(i);
    delay(delayValue);
  }
  }

  if(from < to){
  for(int i=from; i<to; i++){
    servoX.write(i);
    delay(delayValue);
  }
  }
}

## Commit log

2022-10-29 Add board detection with corners
2022-10-30 Add new board detection algorithm
2022-11-02 Add arm directory
2022-11-07 Move camera readme to global readme
2022-11-09 Add Arduino test files
2022-11-09 Add get board image to chess core
2022-11-10 Adding robot arm reference assembly
    [20.5mm Union.SLDPRT, 21mm Union.SLDPRT, 29mm Union.SLDPRT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]
2022-11-10 Adding chess board reference design
    [chess board 1 (x2).stp, chess board 2 (x2).stp, chess board.stp]
2022-11-10 Initial new assembly files
    [20.5mm Union.SLDPRT, 29mm Union.SLDPRT, BackHub .SLDPRT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]
2022-11-10 Add sample env file
2022-11-10 Finalized model of the robot arm setup
    Including the chess board dimensions, the support plate for the robot, and a basic build plate
    [20.5mm Union.SLDPRT, 21mm Union.SLDPRT, 29mm Union.SLDPRT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]
2022-11-11 Add new board moves
2022-11-13 Adding the camera holder
    [CameraBase.SLDPRT]
2022-11-13 Modifying assembly
    [BaseAssembly.SLDPRT, Black squares.SLDPRT, NewAssembly.SLDASM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]
2022-11-13 Generating manufacturing sketches
    [ManufacturingSketches.SLDDRW]
2022-11-17 Update sample env
2022-11-17 Add raise error on using camera
2022-11-17 Fix use camera bug
2022-11-17 Add check if already calibrated
2022-11-18 Dockerize arduino
2022-11-18 Add switch turn logic
2022-11-18 Adjust gripper servo positions
2022-11-18 Add safe pose servo positions
2022-11-18 Add arduino move logic
2022-11-18 Fix bug in arduino code
    [arduino-ros-node.ino]
2022-11-23 Add real board example
2022-11-23 Add camera ros subscriber
2022-11-23 Creating the chess piece part
    [GenericPiece.SLDPRT]
2022-11-23 Create manufacturing sketches of the chess piece part
    [GenericPiece.SLDDRW]
2022-11-23 Generate 3D printing .stl file
    [GenericPiece.STL]
2022-11-23 Modifying holder part
    [CameraHolder.SLDPRT]
2022-11-23 Generate 3D printing .stl file for the holder
    [CameraHolder.STL]
2022-11-30 Rebase and few bug fixes
    [arduino-ros-node.ino]
2022-11-30 Add LED flash for debugging
2022-12-01 Create freedrive python-arduino interface
2022-12-19 Add use previously calibrated board
2022-12-19 Move update chess core board
2022-12-19 Add reverse chess board map
2022-12-19 Do not switch turns if checkmated
2022-12-19 Add empty board
2022-12-19 Move update board lines
2022-12-19 Finalizing CAD branch
    [Bishop.SLDPRT, Bishop.STL, Caballo ajedrez 2D.dwg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]
2022-12-20 Add lab calibration files
